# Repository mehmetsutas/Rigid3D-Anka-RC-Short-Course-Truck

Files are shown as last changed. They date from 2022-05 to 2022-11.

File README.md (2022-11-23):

# RIGID3D ANKA 3d Printed 1/10 RC Short Course Truck
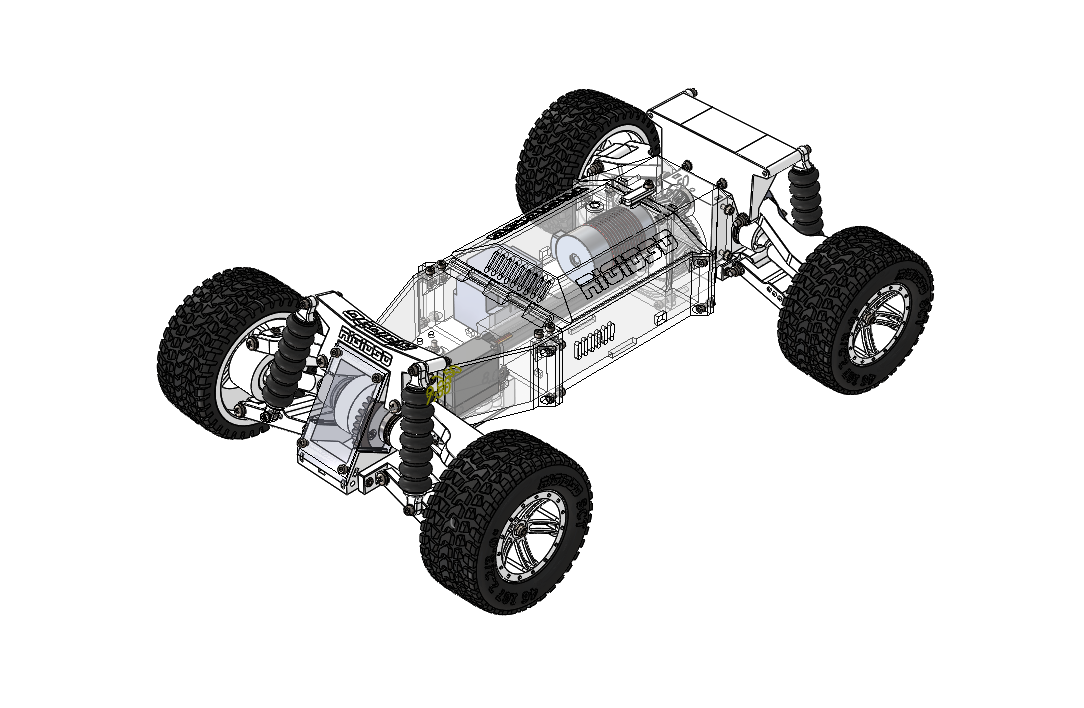
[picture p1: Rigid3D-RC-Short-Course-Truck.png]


Anka is a mostly 3d printed 1/10 RC Short Course Truck which is inspired and remixed from the excellent Tarmo4 project. (You may reach the Tarmo4 project's details from [here](https://www.reddit.com/r/EngineeringNS/).)

If you are a terrible driver like me, this hobby might become a bit expensive. Especially bashers may encounter lots of crashes and breakage which discourages the hobbyist. I wanted to design a basher which is mostly 3d printed so that I can drive it without worrying about crashes and breaks. I enjoy bashing more since I don't have to pay for the spares and wait for them to arrive.

The project is named Anka which is the Turkish equivalent of Phoenix from Greek or Simurgh from Persian mythology. After each crash broken parts are reprinted and the truck is reborn as does the immortal Anka which is reborn from its ashes.

In this model you can even print the shock absorbers and tires with TPU filament. But do not expect the performance of oil filled shocks or rubber tires from them.

Most of the parts may be printed with PLA and should work well with 2600KV motor and 2S LIPO battery. The material tested and recommended are shown in the file notes.

It can be printed on small printers. Most of the parts can be fit in a 15x15x15cm (6"x6"x6") build volume. Only the bumpers require at least 20x20cm (8”x8”) print bed.

The truck is designed in the Short Course Truck (SCT) class. It meets the width and wheelbase dimension specifications of ROAR 1/10 Short Course Truck class.

The steering system is designed according to Ackermann geometry.

3d printed open differentials are used on both front and rear differentials.

Traxxas Slash or Remo Hobby short course truck body would fit on it perfectly. Body can be fixed to the chassis by glueing strong magnets.

You may reach the parametric design files from [github repository](https://github.com/mehmetsutas/Rigid3D-Anka-RC-Short-Course-Truck).

[Here is a test run of Anka.](https://youtu.be/6hFY0XV2smo)

Shield: [][cc-by-sa]

This work is licensed under a
[Creative Commons Attribution-ShareAlike 4.0 International License][cc-by-sa].

[][cc-by-sa]

[cc-by-sa]: http://creativecommons.org/licenses/by-sa/4.0/
[cc-by-sa-image]: https://licensebuttons.net/l/by-sa/4.0/88x31.png
[cc-by-sa-shield]: https://img.shields.io/badge/License-CC%20BY--SA%204.0-lightgrey.svg

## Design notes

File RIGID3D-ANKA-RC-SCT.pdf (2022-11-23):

# RIGID3D ANKA

# 1/10 RC SHORT COURSE TRUCK

English

Version 1.0

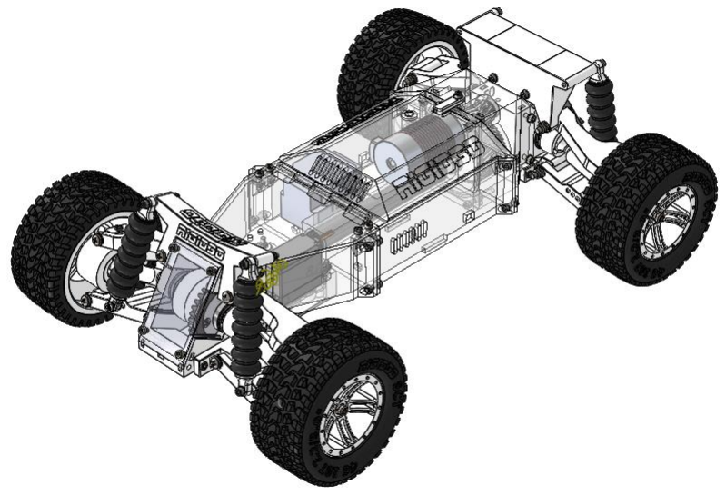
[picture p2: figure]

Rigid3D Anka RC Truck (https://www.rigid3d.com/rigid3d-anka-rc-truck/) © 2022 by Rigid3D is (https://www.rigid3d.com/) licensed under CC BY-SA 4.0 (http://creativecommons.org/licenses/by-sa/4.0/?ref=chooser-v1)

CONTENTS

INTRODUCTION

Anka is a mostly 3d printed 1/10 RC Short Course Truck which is inspired and remixed from the excellent Tarmo4 project. (You may reach the Tarmo4 project's details from here.) (https://www.reddit.com/r/EngineeringNS/)

If you are a terrible driver like me, this hobby might become a bit expensive. Especially bashers may encounter lots of crashes and breakage which discourages the hobbyist. I wanted to design a basher which is mostly 3d printed so that I can drive it without worrying about crashes and breaks. I enjoy bashing more since I don't have to pay for the spares and wait for them to arrive.

The project is named Anka which is the Turkish equivalent of Phoenix from Greek or Simurgh from Persian mythology. After each crash broken parts are reprinted and the truck is reborn as does the immortal Anka which is reborn from its ashes.

In this model you can even print the shock absorbers and tires with TPU filament. But do not expect the performance of oil filled shocks or rubber tires from them.

Most of the parts may be printed with PLA and should work well with 2600KV motor and 2S LIPO battery. The material tested and recommended are shown in the file notes.

It can be printed on small printers. Most of the parts can be fit in a 15x15x15cm (6"x6"x6") build volume. Only the bumpers require at least 20x20cm (8”x8”) print bed.

The truck is designed in the Short Course Truck (SCT) class. It meets the width and wheelbase dimension specifications of ROAR 1/10 Short Course Truck class.

The steering system is designed according to Ackermann geometry.

3d printed open differentials are used on both front and rear differentials.

Traxxas Slash or Remo Hobby short course truck body would fit on it perfectly. Body can be fixed to the chassis by glueing strong magnets.

You may reach the parametric design files from github repository. (https://github.com/mehmetsutas/Rigid3D-Anka-RC-Short-Course-Truck)

LICENSE

Rigid3D Anka RC Truck © 2022 by Rigid3D is licensed under Attribution-ShareAlike 4.0 International. To view a copy of this license, visit http://creativecommons.org/licenses/by-sa/4.0/

LINKS
TARMO4 Project | https://www.reddit.com/r/EngineeringNS/
STL Files | https://www.printables.com/model/214280
GITHUB Repository (STL + Parametric Files) | https://github.com/mehmetsutas/Rigid3D-Anka-RC-Short-Course-Truck
Rigid3D Website (Turkish) | https://www.rigid3d.com
Anka Webpage (under development) | https://www.rigid3d.com/rigid3d-anka-rc-truck/

You may use EngineeringNS subreddit to discuss issues about ANKA along with TARMO4.

SPECIFICATIONS

Class | 1/10 Expert Short Course Truck 4x4
Length | NA (will be available after bumper designs)
Front Track | 296mm (with 3d printed tires)
Rear Track | 296mm (with 3d printed tires)
Center Ground Clearence | 67mm (with 3d printed tires and shocks)
Weight | 2.3kgs (without battery / with 3d printed tires and shocks)
Height | NA (depends on body)
Wheelbase | 321mm
Tire Diameter / Width | 107mm / 46mm
Wheel Diameter | Outer 56mm, Inner 76mm
Drive Ratio | Gearbox 2.625, Differential 2.5, Total 6,5625
Differential | Front & rear 3d printed open type
Drive | Shaft driven
Theoretical Steering Angle | Max. 30˚ (depends on the servo angle. 180˚ servo may steer upto around 27˚)
Caster | 15˚ Positive
Camber | Neutral
Toe | Front Zero, Rear 2.5˚ Toe-in
Battery Compartment Dim. | 122x40x43mm
ESC Compartment Dim. | (122 – Motor Body Length)x40x43mm
Motor Mount | Suitable for Φ36mm brushless or 540/550 brushed motor (Max motor body length 78mm)
Recommended Motor | Brushless 2600KV or lower KV / Brushed 35T or higher turns
Servo Mount Dimensions | 40x20mm servo, distance between mount holes 49x10mm

NEEDED TOOLS

- PH1 Screw Driver
- 5.5 and 7mm Wrench
- 2.5mm Allen Wrench (A short and a long one with ball head is recommended)
- 7mm Socket Wrench (for tightening wheel nuts)
- Drill & 2.5, 3, 4mm drill Bits
- M3 Tap (Optional. There are only a few screws that are directly screwed on plastic.)
- 200 grit sand paper (For cleaning the bearing fit surfaces)
- Hacksaw (for cutting 3mm rod to length)

CONSUMABLES

- PLA filament (more than 1 kg)
- PA12 filament (optional)
- TPU filament
- CA glue
- NLGI00 grade lithium grease⁽*)

(*) NLGI grade determines the viscosity of the grease. 00 grade is low viscous. While NLGI3 grease is like a soap, NLGI00 is like thin jam. It is mainly used in machines with automatic oil pumps for lubricating the linear rails, gears and bearings. It would be hard (at least in Turkey) to find it in small volumes. It is sold in barrels or buckets. But you can produce your own low viscosity grease by mixing a small amount NLGI 2-3 lithium grease with general purpose machine oil or engine oil. The thickness should be like jam. You can use the same mixture to lubricate the linear rails and linear bearings of the 3d printer.

NON-PRINTED PARTS BOM

ITEM NO. | PART | SPECIFICATION | QTY
82 | motor | | 1
102 | servo | | 1
126 | esc | | 1
4/15/37/62/83/117 | 6700 - 15x10x4 bearıng | | 18
13 | 6802 - 15x24x5 bearing | | 4
| Φ3mm steele rod | | 1 meter
30 | wheel-shaft-strength-bar | Φ3mm x 60mm | 4
91 | drive-shaft-strength-bar | Φ3mm x 160mm | 1
2 | planet-gear-pın | Φ3mm x 28mm | 12
24 | shock-pin | Φ3mm x 40mm | 4
105 | rod-ball / 8mm metal bead with 3mm hole | | 4
7/115 | countersunk flat head cross recess screw_ıso | M3 X 30 | 9
103 | countersunk flat head cross recess screw_iso | M3 X 10 | 1
114/138 | countersunk flat head cross recess screw_iso | M3 X 12 | 5
113 | countersunk flat head cross recess screw_iso | M3 X 16 | 2
19/112 | countersunk flat head cross recess screw_iso | M3 X 25 | 6
86/122 | countersunk flat head cross recess screw_iso | M3 X 8 | 10
8/18/52/88/109/129/143/148 | hex nut style 1 gradeab_ıso | M3 | 81
57 | hex nut style 1 gradeab_iso | M4 | 8
55/72 | hex screw gradeab_iso | M4 X 30 | 4
48 | pan head cross recess screw_iso | M4 X 16 | 8
43/79 | pan head cross recess screw_iso | M4 X 35 | 4
58/78 | pan head cross recess screw_iso_2 | M4 X 45 | 8
10/42/75/96/107 | plaın washer normal grade a_ıso | 3 | 62
41/71 | plain washer normal grade a_iso | 4 | 29
20/94/108/127 | socket head cap screw_iso | M3 X 10 | 23
54/74/89/97/123/130/142/147 | socket head cap screw_iso | M3 X 12 | 38
28/51/76/99 | socket head cap screw_iso | M3 X 16 | 17
139 | socket head cap screw_iso | M3 X 20 | 6
45/77 | socket head cap screw_iso | M3 X 25 | 6
44 | socket head cap screw_iso | M3 X 30 | 2
87 | socket set screw cup point_iso | M4 X 5 | 1
9/29/46/121 | torque nut 08_ıso | M3 | 31
47/73 | torque nut 08_iso | M4 | 16
Use any 540/550 sized 35T or higher turn brushed motor or any 2600KV or lower KV Φ36mm inrunner brushless motor. (https://www.aliexpress.com/item/32964687978.html)

For rod balls, stainless steel beads for jewelry making may be used or the balls can be printed. STL for the rod balls can be found at extras folder. (https://www.aliexpress.com/item/33012805327.html)

Links are given for information. Do not consider them as best option.

PRINTED PARTS BOM & PRINT SETTINGS

ITEM NO. | PART | QTY | HEIGHT LAYER | S | INFILL | WALL THICKNESS | MAT. | ORIENTATION
36/63 | axle | 4 | 0,2mm | N | 10 | 3,2mm | PLA
110 | chassis-front | 1 | 0,3mm | N | 10 | 1,6mm | PLA

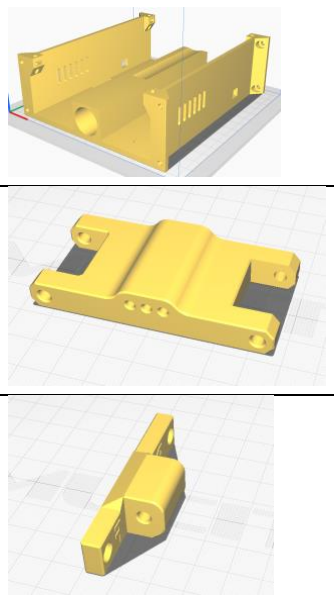
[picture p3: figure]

93 | chassis-middle | 1 | 0,3mm | N | 10 | 1,6mm | PLA
60 | control-arm-lower-BACK | 2 | 0,2mm | N | 10 | 3,2mm | PLA
70 | control-arm-lower-bracket-back-left | 1 | 0,2mm | N | 10 | 3,2mm | PLA (PA12)
69 | control-arm-lower-bracket-back-right | 1 | 0,2mm | N | 10 | 3,2mm | PLA (PA12)
49 | control-arm-lower-bracket-front-left | 1 | 0,2mm | N | 10 | 3,2mm | PLA (PA12)
50 | control-arm-lower-bracket-front-right | 1 | 0,2mm | N | 10 | 3,2mm | PLA (PA12)

ITEM NO. | PART | QTY | HEIGHT LAYER | S | INFILL | WALL THICKNESS | MAT. | ORIENTATION
34 | control-arm-lower-FRONT | 2 | 0,2mm | N | 10 | 3,2mm | PLA

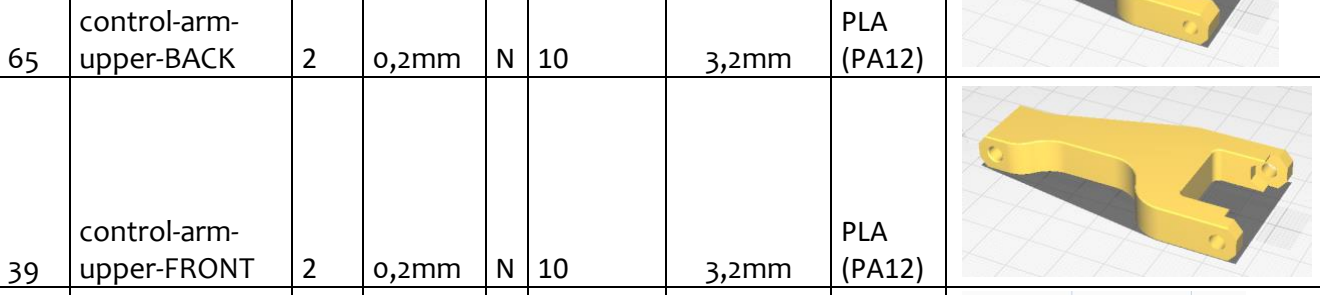
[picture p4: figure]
control-arm-upper-BACK; PLA (PA12); control-arm-upper-FRONT

128 | cover-front | 1 | 0,3mm | N | 10 | 1,6mm | PLA
131 | cover-middle | 1 | 0,3mm | Y | 10 | 1,6mm | PLA
1 | dıfferentıal-housıng-a | 2 | 0,2mm | N | 10 | 3,2mm | PLA
6 | dıfferentıal-housıng-b | 2 | 0,2mm | N | 10 | 3,2mm | PLA
11 | differential-box | 2 | 0,3mm | N | 10 | 1,6mm | PLA

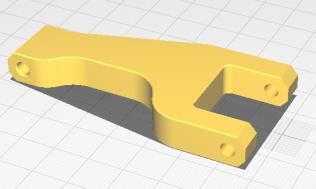
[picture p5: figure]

ITEM NO. | PART | QTY | HEIGHT LAYER | S | INFILL | WALL THICKNESS | MAT. | ORIENTATION
14 | differential-box-lid | 2 | 0,3mm | N | 10 | 1,6mm | PLA
16 | drive-pinion-gear | 2 | 0,2mm | N | 10 | 3,2mm | PLA
90 | drive-shaft | 1 | 0,2mm | N | 10 | 3,2mm | TPU
80 | gear-box | 1 | 0,3mm | N | 10 | 1,6mm | PLA
81 | gear-box-lid | 1 | 0,3mm | N | 10 | 1,6mm | PLA
61 | knuckle-rear | 2 | 0,2mm | N | 10 | 3,2mm | PLA
100 | lock-bar | 1 | 0,2mm | N | 10 | 1,6mm | PLA
3 | planet-gear | 12 | 0,2mm | N | 10 | 3,2mm | PLA

ITEM NO. | PART | QTY | HEIGHT LAYER | S | INFILL | WALL THICKNESS | MAT. | ORIENTATION
25 | rim | 4 | 0,25mm | Y | 10 | 1,6mm | PLA
116 | rod-ball-spacer | 2 | 0,2mm | N | 10 | 1,6mm | PLA
111 | servo-cover | 1 | 0,3mm | N | 10 | 1,6mm | PLA
104 | servo-saver | 1 | 0,2mm | N | 10 | 3,2mm | PLA
119 | servo-saver-SLAVE | 1 | 0,2mm | N | 10 | 3,2mm | PLA
118 | servo-saver-washer | 1 | 0,2mm | N | 10 | 1,6mm | PLA
84 | sg-16-1 | 1 | 0,2mm | N | 10 | 3,2mm | PLA
85 | sg-42-1 | 1 | 0,2mm | N | 10 | 3,2mm | PLA

ITEM NO. | PART | QTY | HEIGHT LAYER | S | INFILL | WALL THICKNESS | MAT. | ORIENTATION
5 | shaft-gear | 4 | 0,2mm | N | 10 | 3,2mm | PLA
23 | shock-eye-A | 4 | 0,2mm | N | 10 | 3,2mm | PLA
22 | shock-eye-B | 4 | 0,2mm | N | 10 | 3,2mm | PLA
66 | shock-tower-back | 1 | 0,3mm | N | 10 | 1,6mm | PLA

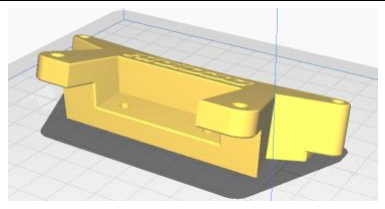
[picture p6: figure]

53 | shock-tower-front | 1 | 0,3mm | Y | 10 | 1,6mm | PLA
120 | steering-center-link | 1 | 0,2mm | N | 10 | 3,2mm | PLA

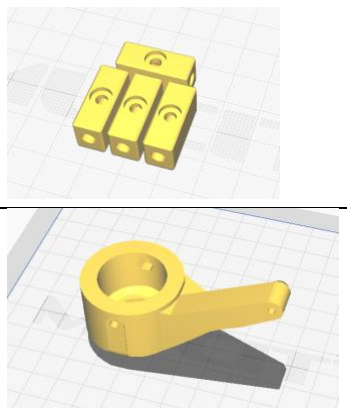
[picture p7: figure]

33 | steering-knuckle-bracket | 4 | 0,2mm | N | 10 | 3,2mm | PLA
32 | steering-knuckle-left | 1 | 0,2mm | N | 10 | 3,2mm | PLA

ITEM NO. | PART | QTY | HEIGHT LAYER | S | INFILL | WALL THICKNESS | MAT. | ORIENTATION
56 | steering-knuckle-right | 1 | 0,2mm | N | 10 | 3,2mm | PLA
106 | steering-linkage⁽*) | 2 | 0,2mm | N | 10 | 3,2mm | PLA

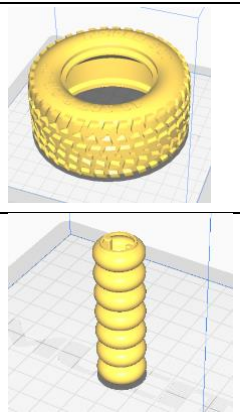
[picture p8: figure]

26 | tire | 4 | 0,25mm | N | 10 | 1,6mm | TPU
21 | tpu-spring | 4 | 0,2mm | N | 10 | 1,6mm | TPU
27 | wheel-shaft | 4 | 0,2mm | N | 10 | 3,2mm | PLA

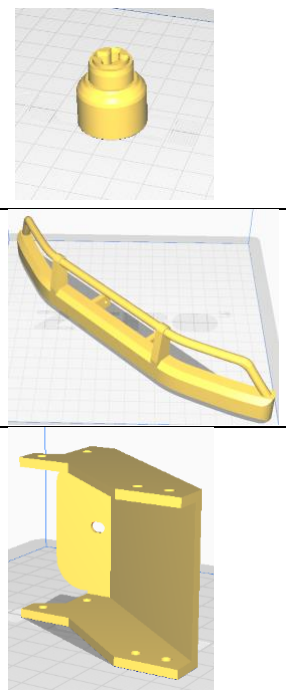
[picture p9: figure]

17 | wheel-shaft-housing | 4 | 0,2mm | N | 10 | 3,2mm | PLA
140 | bumper-bottom-front | 1 | 0,3mm | Y | 10 | 2mm | PLA
141 | bumper-bracket-front | 1 | 0,3mm | Y | 10 | 2mm | PLA

ITEM NO. | PART | QTY | HEIGHT LAYER | S | INFILL | WALL THICKNESS | MAT. | ORIENTATION

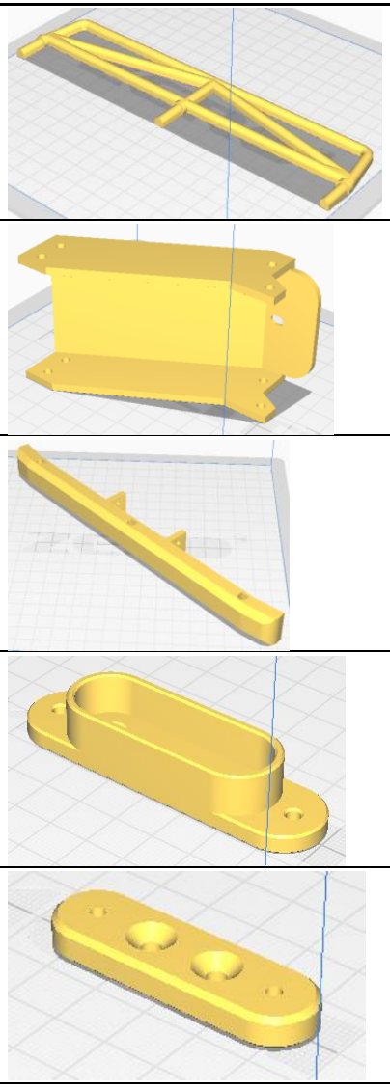
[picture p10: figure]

144 | bumper-rail-back | 1 | 0,2mm | N | 10 | 2mm | PLA
145 | bumper-bracket-back | 1 | 0,3mm | Y | 10 | 2mm | PLA
146 | bumper-bottom-back | 1 | 0,3mm | N | 10 | 2mm | PLA
132 | body-mount-front | 1 | 0,3mm | N | 10 | 2mm | PLA
133 | body-mount-front-body-bracket | 1 | 0,3mm | N | 10 | 2mm | PLA
134 | body-mount-rear | 1 | 0,3mm | N | 10 | 2mm | PLA
135 | body-mount-rear-body-bracket | 1 | 0,3mm | N | 10 | 2mm | PLA

S: Support Needed? Y=Yes / N=No -- MAT.: Material

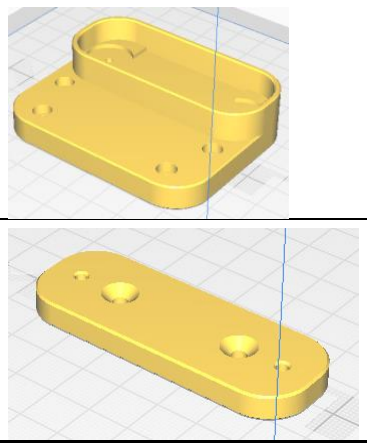
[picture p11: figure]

Although PLA is sufficient for most of the parts on normal operation of the car. It is seen that some parts tend to break more frequently on crashes. It is recommended to print these parts with a nylon blend such as PA12. PA12 is shown in parenthesis as material for these parts.

(*) Print steering linkage in 2 pieces by lowering the model 2.5mm in Z direction into the print bed. Combine 2 halves by screws and nuts after placing the rod balls on the recesses.

EXPLODED DRAWINGS

DIFFERENTIAL INNER ASSY

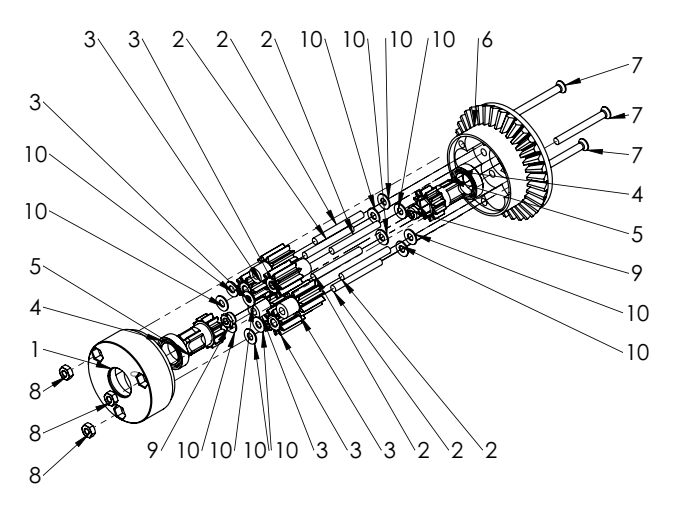
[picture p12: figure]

ITEM NO. | PART | SPECIFICATION | QTY.
1 | dıfferentıal-housıng-a | | 1
2 | planet-gear-pın | Φ3mm x 28mm | 6
3 | planet-gear | | 6
4 | 6700 - 15x10x4 bearıng | | 2
5 | shaft-gear | | 2
6 | dıfferentıal-housıng-b | | 1
7 | countersunk flat head cross recess screw_ıso | M3 X 30 | 3
8 | hex nut style 1 gradeab_ıso | M3 | 3
9 | torque nut 08_ıso | M3 | 2
10 | plaın washer normal grade a_ıso | 3 | 12

Note:

Fill the housing with NLGI00 grade grease.

DIFFERENTIAL ASSY

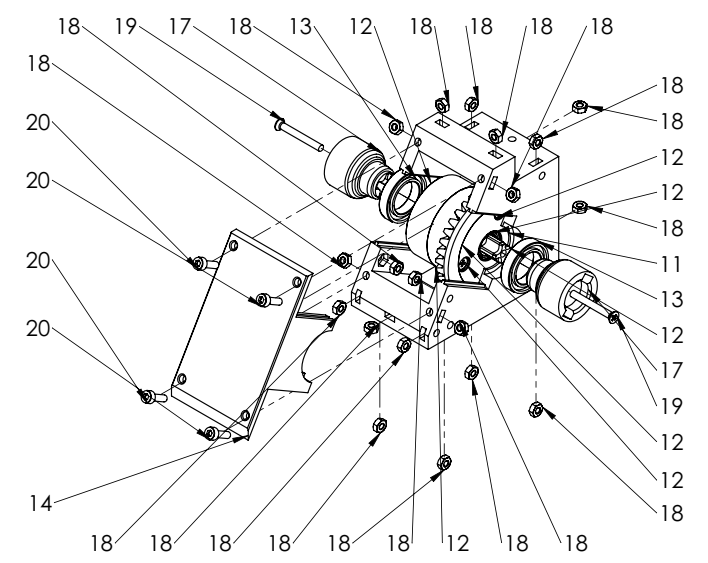
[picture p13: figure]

ITEM NO. | PART | SPECIFICATION | QTY.
11 | differential-box | | 1
12 | differential-inner-assy | | 1
13 | radial ball bearing_68_iso | 15X24X5MM 6802 | 2
14 | differential-box-lid | | 1
15 | 6700 - 15x10x4 Bearing | | 1
16 | drive-pinion-gear | | 1
17 | wheel-shaft-housing | | 2
18 | hex nut style 1 gradeab_iso | M3 | 21
19 | countersunk flat head cross recess screw_iso | M3 X 25 | 2
20 | socket head cap screw_iso | M3 X 10 | 4

Note:

Apply NLGI00 grade grease on the bevel gears.

SHOCK ASSY

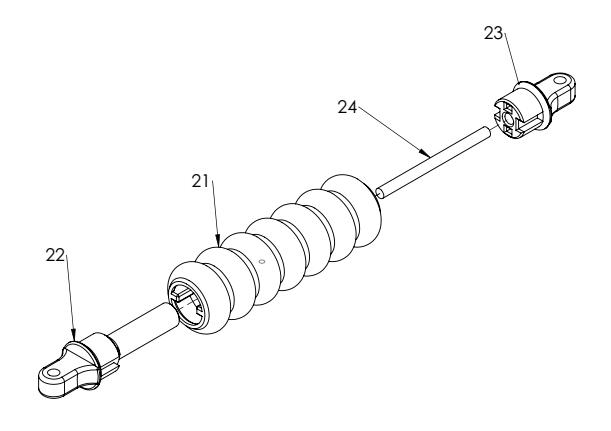
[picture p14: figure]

ITEM NO. | PART | SPECIFICATION | QTY.
21 | tpu-spring | | 1
22 | shock-eye | B | 1
23 | shock-eye | A | 1
24 | shock-pin | Φ3mm x 40mm | 1

Note:

Glue the parts. Pin to shock-eye-A. Shock eyes to tpu-spring.

WHEEL ASSY

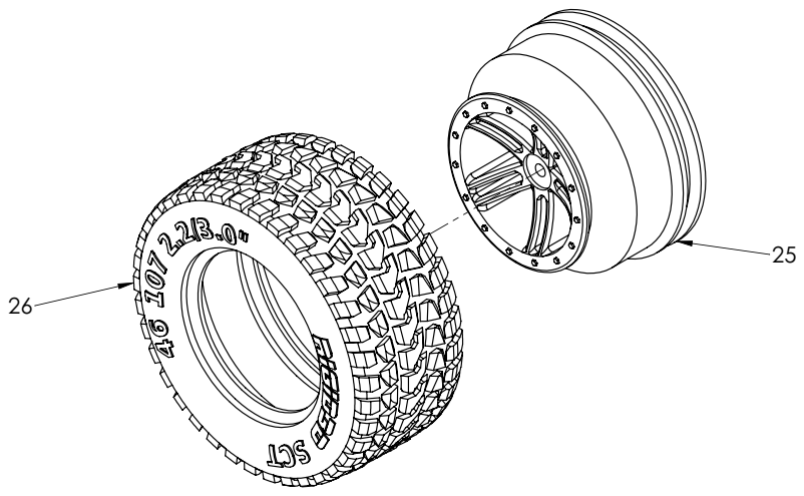
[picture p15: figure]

ITEM NO. | PART | SPECIFICATION | QTY.
25 | rim | | 1
26 | tire | | 1

Notes:

Rim and tire fit very tightly and it requires a lot of force to assemble them together. You may try stepping on the sides of the tire to slide them onto the rim.

WHEEL SHAFT ASSY

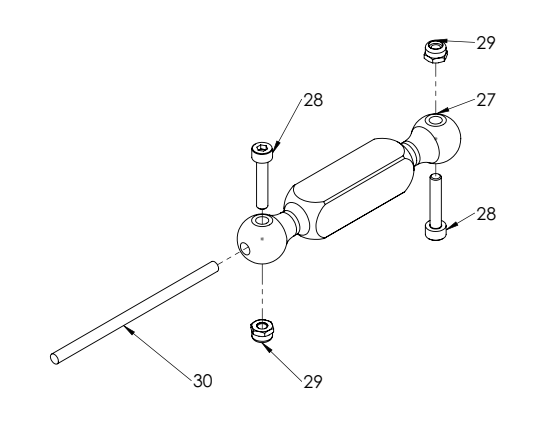
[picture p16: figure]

ITEM NO. | PART | SPECIFICATION | QTY.
27 | wheel-shaft | | 1
28 | socket head cap screw_iso | M3 X 16 | 2
29 | torque nut 08_iso | M3 | 2
30 | wheel-shaft-strength-bar | Φ3mm x 60mm | 1

FRONT ASSY

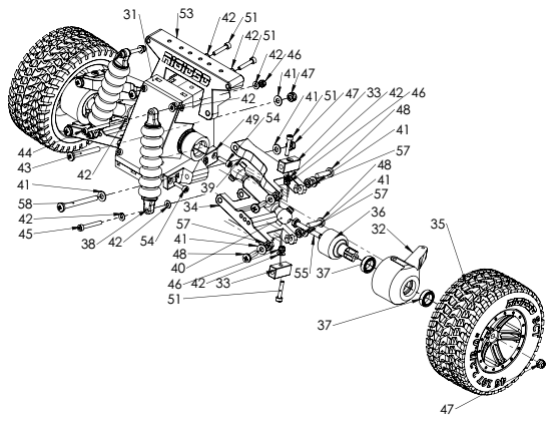
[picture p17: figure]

Notes:

- Only one side is exploded for constraining the sketch size.
- For ease of work, assemble the tires in the last step. Do not install them at this stage of the assembly.

ITEM NO. | PART | SPECIFICATION | QTY.
31 | differential-assy | | 1
32 | steering-knuckle-left | | 1
33 | steering-knuckle-bracket | | 4
34 | control-arm-lower-FRONT | FRONT | 2
35 | wheel-assy | | 2
36 | axle | | 2
37 | 6700 - 15x10x4 Bearing | | 4
38 | shock-assy-V2 | | 2
39 | control-arm-upper-FRONT | FRONT | 2
40 | wheel-shaft-assy | | 2
41 | plain washer normal grade a_iso | 4 | 13
42 | plain washer normal grade a_iso | 3 | 17
43 | pan head cross recess screw_iso | M4 X 35 | 2
44 | socket head cap screw_iso | M3 X 30 | 2
45 | socket head cap screw_iso | M3 X 25 | 2
46 | torque nut 08_iso | M3 | 6
47 | torque nut 08_iso | M4 | 6
48 | pan head cross recess screw_iso | M4 X 16 | 8
49 | control-arm-lower-bracket-front-left | | 1
50 | control-arm-lower-bracket-front-right | | 1
51 | socket head cap screw_iso | M3 X 16 | 6
52 | hex nut style 1 gradeab_iso | M3 | 2
53 | shock-tower-front | | 1
54 | socket head cap screw_iso | M3 X 12 | 4
55 | hex screw gradeab_iso | M4 X 30 | 2
56 | steering-knuckle-right | | 1
57 | hex nut style 1 gradeab_iso | M4 | 8
58 | pan head cross recess screw_iso_2 | M4 X 45 | 2

BACK ASSY

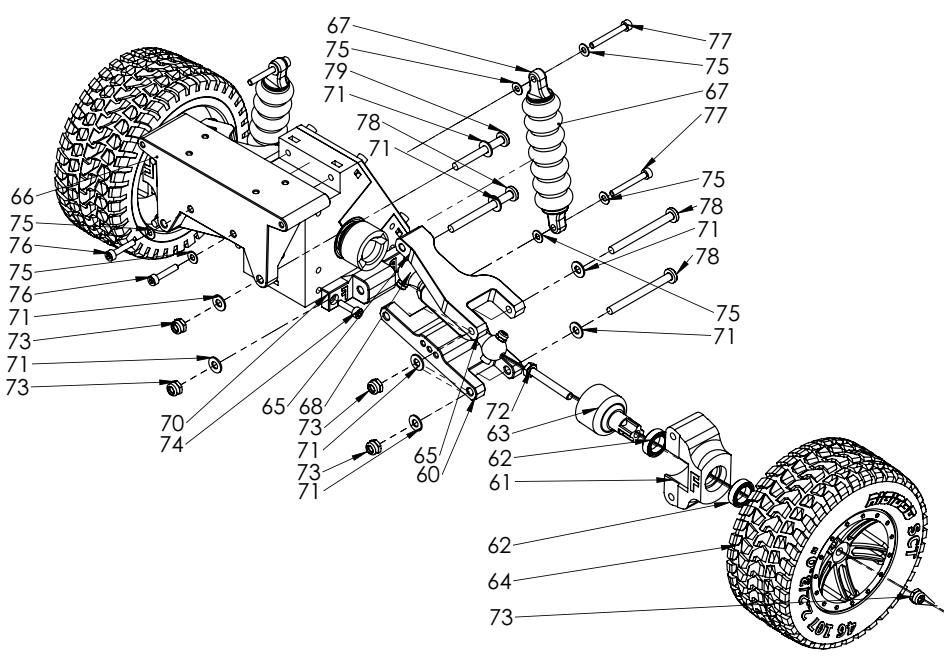
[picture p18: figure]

Notes:

- Only one side is exploded for constraining the sketch size.
- For ease of work, assemble the tires in the last step. Do not install them at this stage of the assembly.

ITEM NO. | PART | SPECIFICATION | QTY.
59 | differential-assy | | 1
60 | control-arm-lower-BACK | BACK | 2
61 | knuckle-rear | | 2
62 | 6700 - 15x10x4 Bearing | | 4
63 | axle | | 2
64 | wheel-assy | | 2
65 | control-arm-upper-BACK | BACK | 2
66 | shock-tower-back | | 1
67 | shock-assy-V2 | | 2
68 | wheel-shaft-assy | | 2
69 | control-arm-lower-bracket-back-right | | 1
70 | control-arm-lower-bracket-back-left | | 1
71 | plain washer normal grade a_iso | 4 | 16
72 | hex screw gradeab_iso | M4 X 30 | 2
73 | torque nut 08_iso | M4 | 10
74 | socket head cap screw_iso | M3 X 12 | 4
75 | plain washer normal grade a_iso | 3 | 10
76 | socket head cap screw_iso | M3 X 16 | 2
77 | socket head cap screw_iso | M3 X 25 | 4
78 | pan head cross recess screw_iso_2 | M4 X 45 | 6
79 | pan head cross recess screw_iso_2 | M4 X 35 | 2

GEAR BOX ASSY

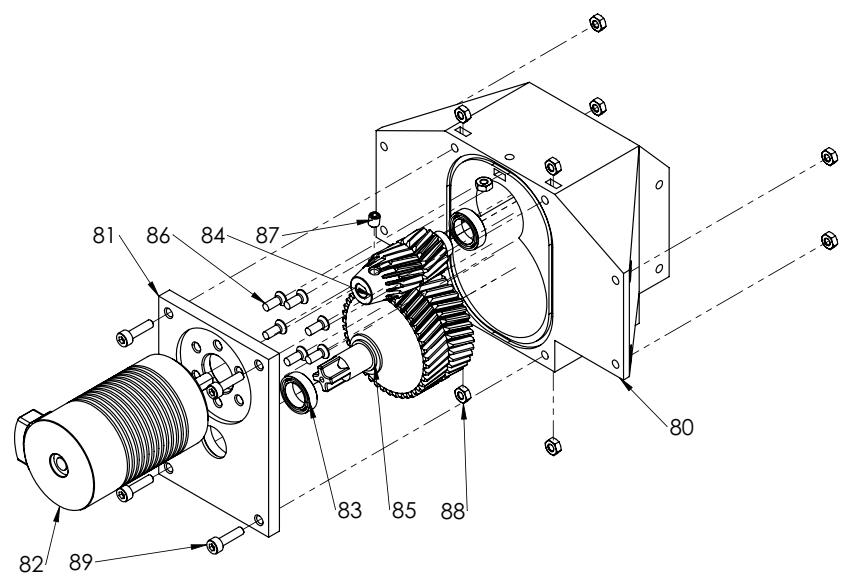
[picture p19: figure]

ITEM NO. | PART | SPECIFICATION | QTY.
80 | gear-box | | 1
81 | gear-box-lid | | 1
82 | motor | | 1
83 | 6700 - 15x10x4 Bearing | | 2
84 | sg-16-1 | 16T-M1 | 1
85 | sg-42-1 | 42T-M1 | 1
86 | countersunk flat head cross recess screw_iso | M3 X 8 | 6
87 | socket set screw cup point_iso | M4 X 5 | 1
88 | hex nut style 1 gradeab_iso | M3 | 9
89 | socket head cap screw_iso | M3 X 12 | 4

Note:

Apply NLGI00 grade grease on the gears.

DRIVE SHAFT ASSY

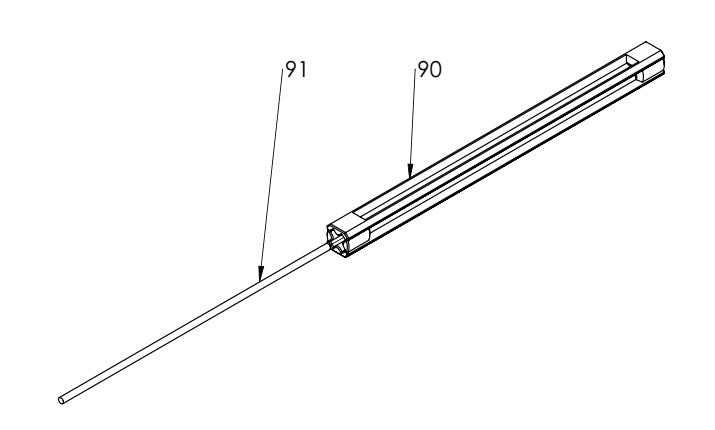
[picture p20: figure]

ITEM NO. | PART | SPECIFICATION | QTY.
90 | drive-shaft | | 1
91 | drive-shaft-strength-bar | Φ3mm x 160mm | 1

RIGID3D SCT BACK ASSY

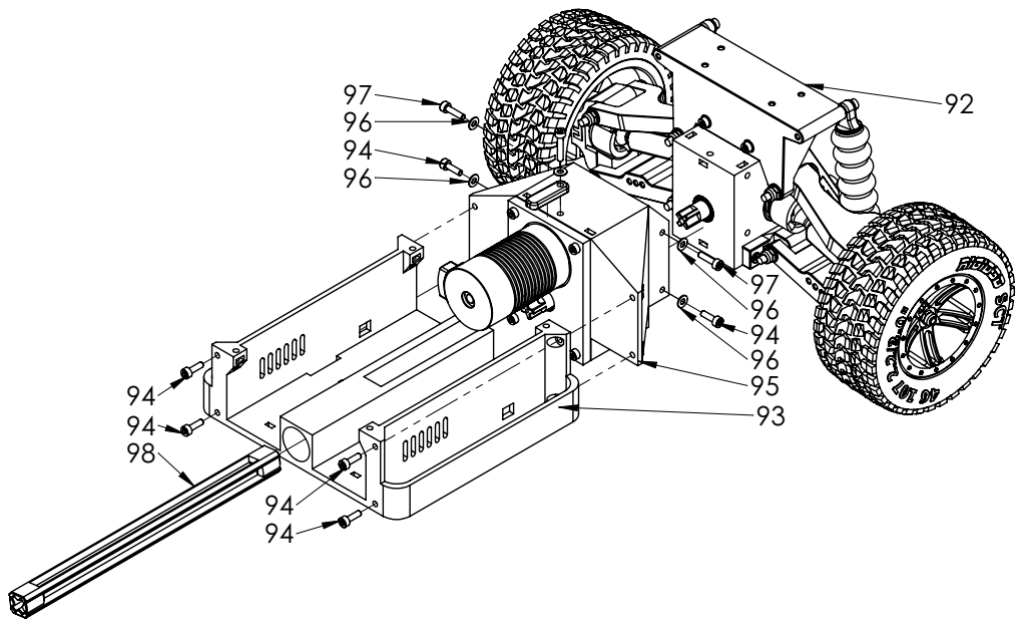
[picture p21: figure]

ITEM NO. | PART | SPECIFICATION | QTY.
92 | back-assy | | 1
93 | chassis-middle | | 1
94 | socket head cap screw_iso | M3 X 10 | 6
95 | gear-box-assy | | 1
96 | plain washer normal grade a_iso | 3 | 5
97 | socket head cap screw_iso | M3 X 12 | 2
98 | drive-shaft-assy | | 1
99 | socket head cap screw_iso | M3 X 16 | 1
100 | lock-bar | | 1

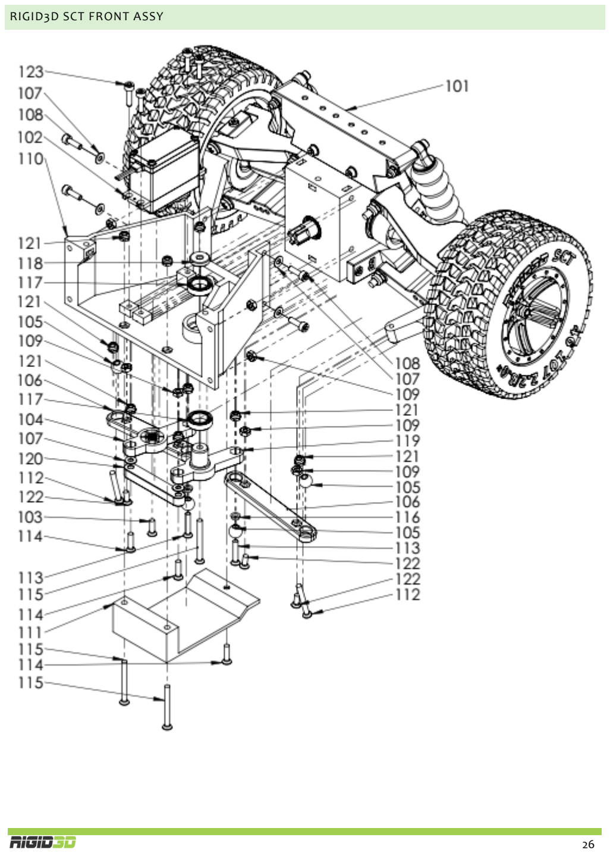
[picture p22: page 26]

RIGID3D SCT FRONT ASSY

ITEM NO. | PART | SPECIFICATION | QTY.
101 | front-assy | | 1
102 | servo | | 1
103 | countersunk flat head cross recess screw_iso | M3 X 10 | 1
104 | servo-saver | | 1
105 | rod-ball | | 4
106 | steering-linkage | | 2
107 | plain washer normal grade a_iso | 3 | 6
108 | socket head cap screw_iso | M3 X 10 | 4
109 | hex nut style 1 gradeab_iso | M3 | 8
110 | chassis-front | | 1
111 | servo-cover | | 1
112 | countersunk flat head cross recess screw_iso | M3 X 25 | 2
113 | countersunk flat head cross recess screw_iso | M3 X 16 | 2
114 | countersunk flat head cross recess screw_iso | M3 X 12 | 3
115 | countersunk flat head cross recess screw_iso | M3 X 30 | 3
116 | rod-ball-spacer | | 2
117 | 6700 - 15x10x4 Bearing | | 2
118 | servo-saver-washer | | 1
119 | servo-saver-SLAVE | SLAVE | 1
120 | steering-center-link | | 1
121 | torque nut 08_iso | M3 | 13
122 | countersunk flat head cross recess screw_iso | M3 X 8 | 4
123 | socket head cap screw_iso | M3 X 12 | 4

RIGID3D SCT V2

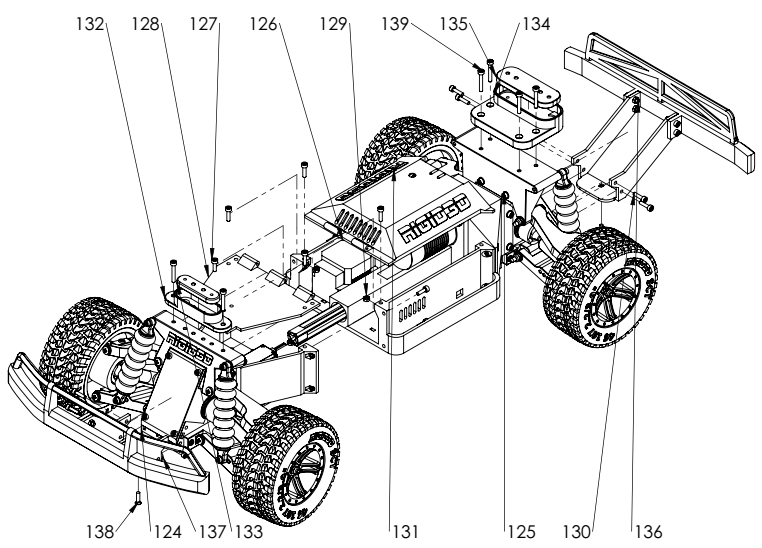
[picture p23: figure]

ITEM NO. | PART | SPECIFICATION | QTY.
124 | rigid3d-sct-front-assy | | 1
125 | rigid3d-sct-back-assy | | 1
126 | esc | | 1
127 | socket head cap screw_iso | M3 X 10 | 5
128 | cover-front | | 1
129 | hex nut style 1 gradeab_iso | M3 | 6
130 | socket head cap screw_iso | M3 X 12 | 12
131 | cover-middle | | 1
132 | body-mount-front | | 1
133 | body-mount-front-body-bracket | | 1
134 | body-mount-rear | | 1
135 | body-mount-rear-body-bracket | | 1
136 | bumper-back | | 1
137 | bumper-front | | 1
138 | countersunk flat head cross recess screw_iso | M3 X 12 | 2
139 | socket head cap screw_iso | M3 X 20 | 6

Note:

Middle cover is hinged. Use a piece of 1.75mm filament as hinge pin.

BUMPER FRONT

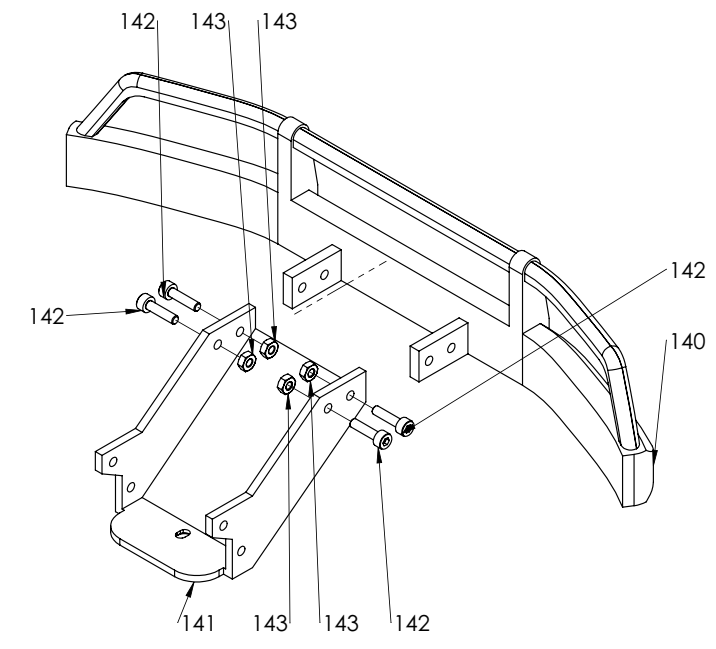
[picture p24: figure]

ITEM NO. | PART | SPECIFICATION | QTY.
140 | bumper-bottom-front | | 1
141 | bumper-bracket-front | | 1
142 | socket head cap screw_iso | M3 X 12 | 4
143 | hex nut style 1 gradeab_iso | M3 | 4

BUMPER BACK

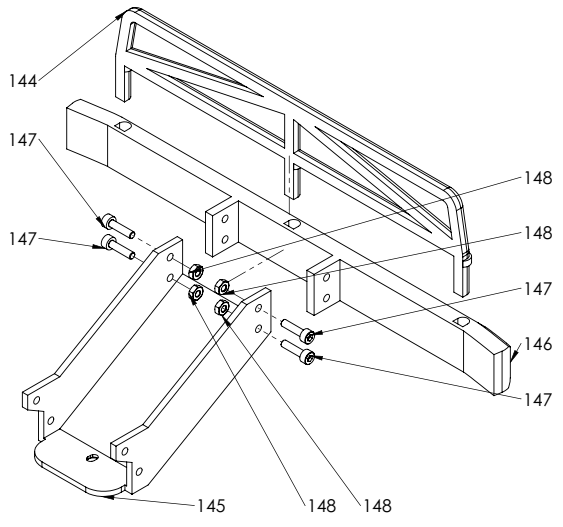
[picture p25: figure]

ITEM NO. | PART | SPECIFICATION | QTY.
144 | bumper-rail-back | | 1
145 | bumper-bracket-back | | 1
146 | bumper-bottom-back | | 1
147 | socket head cap screw_iso | M3 X 12 | 4
148 | hex nut style 1 gradeab_iso | M3 | 4

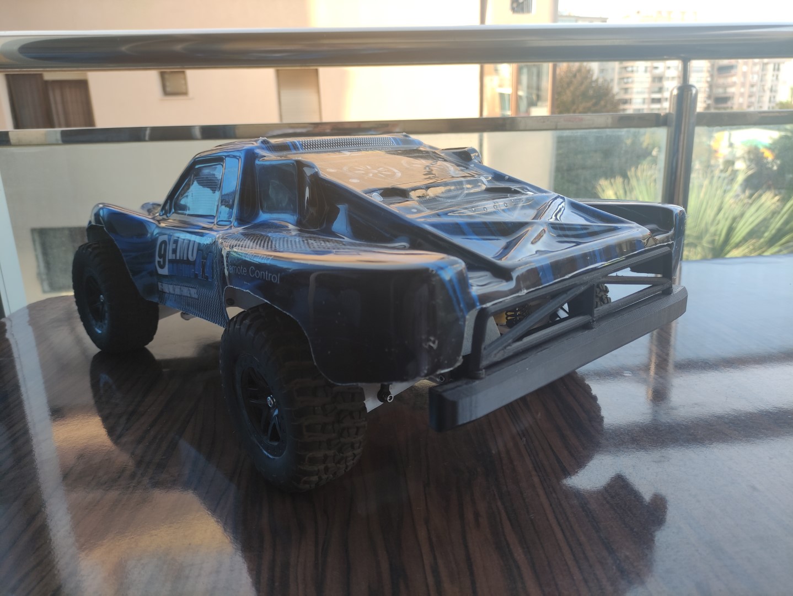
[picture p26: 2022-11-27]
IMG_20221001_175840 (Büyük).jpg

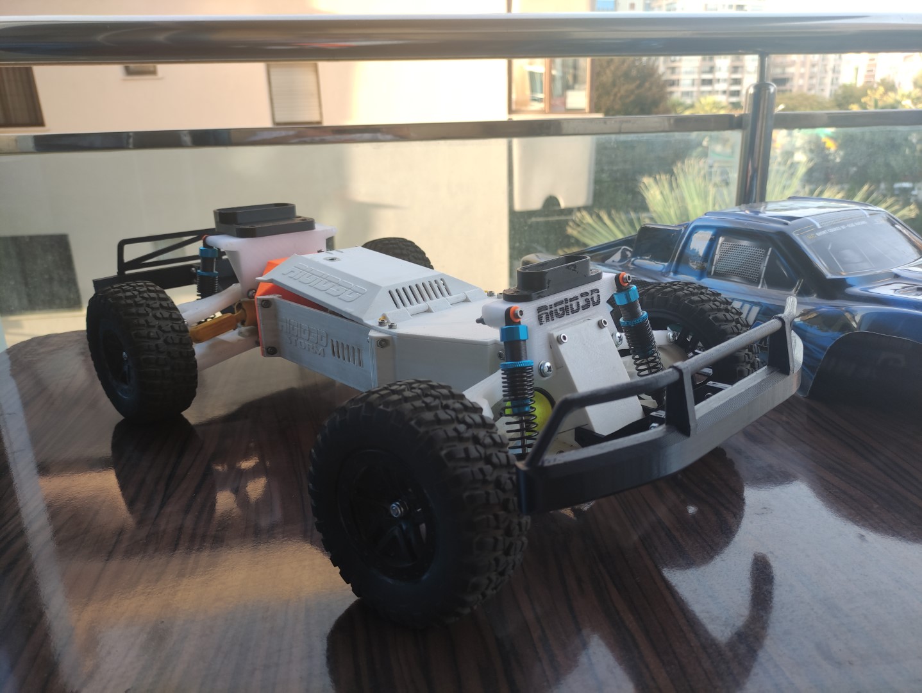
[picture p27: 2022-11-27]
IMG_20221001_175925 (Büyük).jpg

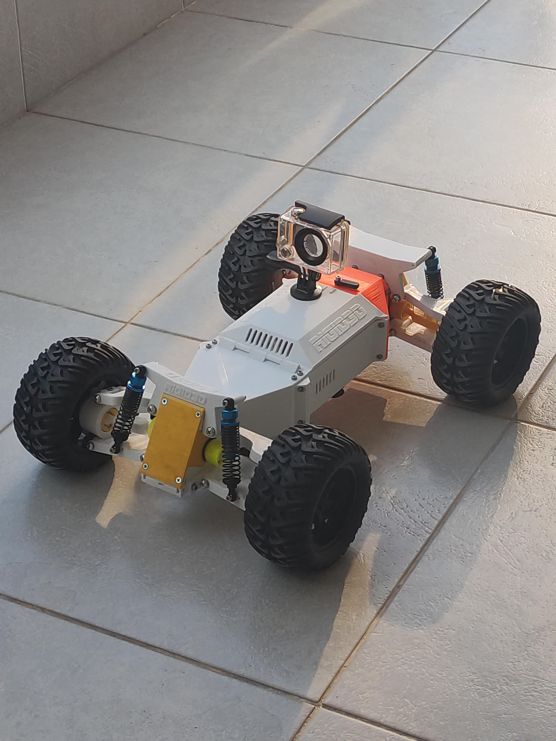
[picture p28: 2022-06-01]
pmxta5gfsnz81.jpg

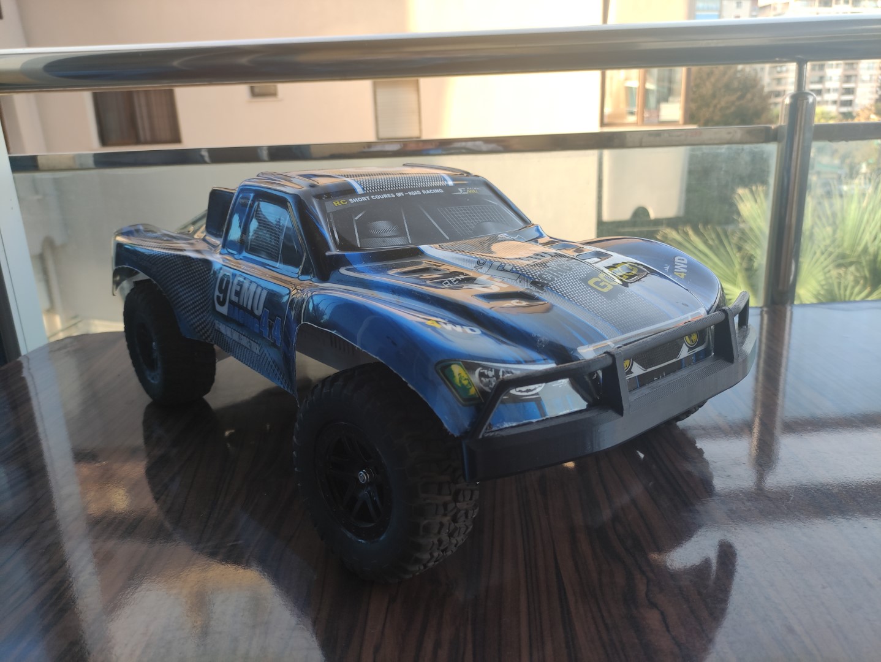
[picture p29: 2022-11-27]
IMG_20221001_175818 (Büyük).jpg

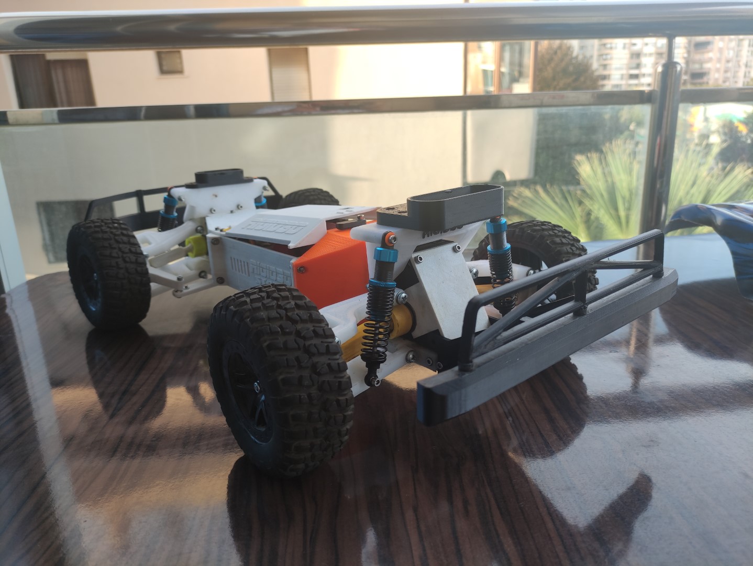
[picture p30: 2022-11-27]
IMG_20221001_175855 (Büyük).jpg

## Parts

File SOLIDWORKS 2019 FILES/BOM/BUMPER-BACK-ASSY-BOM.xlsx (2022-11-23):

ITEM NO. | PART | SPECIFICATION | QTY. | SW-Configuration Name(Configuration Name)
144 | bumper-rail-back |  | 1 | Default
145 | bumper-bracket-back |  | 1 | Default
146 | bumper-bottom-back |  | 1 | Default
147 | socket head cap screw_iso | M3 X 12 | 4 | ISO 4762 M3 x 12 - 12N
148 | hex nut style 1 gradeab_iso | M3 | 4 | ISO - 4032 - M3 - D - N

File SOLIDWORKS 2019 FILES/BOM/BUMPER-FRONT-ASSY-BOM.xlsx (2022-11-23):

ITEM NO. | PART | SPECIFICATION | QTY. | SW-Configuration Name(Configuration Name)
140 | bumper-bottom-front |  | 1 | Default
141 | bumper-bracket-front |  | 1 | Default
142 | socket head cap screw_iso | M3 X 12 | 4 | ISO 4762 M3 x 12 - 12N
143 | hex nut style 1 gradeab_iso | M3 | 4 | ISO - 4032 - M3 - D - N

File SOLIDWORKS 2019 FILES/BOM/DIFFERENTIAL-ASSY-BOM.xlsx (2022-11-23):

ITEM NO. | PART | SPECIFICATION | QTY. | SW-Configuration Name(Configurat ion Name)
11 | differential-box |  | 1 | Default
12 | differential-inner-assy |  | 1 | Default
13 | radial ball bearing_68_iso | 15X24X5MM 6802 | 2 | ISO 15 RBB - 1815 - 18,SI,NC,18_68
14 | differential-box-lid |  | 1 | Default
15 | 6700 - 15x10x4 Bearing |  | 1 | Rolling bearings 63700 GB 276-94
16 | drive-pinion-gear |  | 1 | ISO - Straight bevel pinion 1.5M14PT 37GT 20PA 7FW --- 14O9,9H32MD2.0 N
17 | wheel-shaft-housing |  | 2 | Default
18 | hex nut style 1 gradeab_iso | M3 | 21 | ISO - 4032 - M3 - D - N
19 | countersunk flat head cross recess screw_iso | M3 X 25 | 2 | ISO 7046-1 - M3 x 25 - Z - 25N
20 | socket head cap screw_iso | M3 X 10 | 4 | ISO 4762 M3 x 10 - 10N

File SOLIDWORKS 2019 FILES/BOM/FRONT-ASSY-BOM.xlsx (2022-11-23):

ITEM NO. | PART | SPECIFICATION | QTY. | SW-Configuration Name(Configuration Name)
31 | differential-assy |  | 1 | Default
32 | steering-knuckle-left |  | 1 | Default
33 | steering-knuckle-bracket |  | 4 | Default
34 | control-arm-lower |  | 2 | on
35 | wheel-assy |  | 2 | Default
36 | axle |  | 2 | Default
37 | 6700 - 15x10x4 Bearing |  | 4 | Rolling bearings 63700 GB 276-94
38 | shock-assy-V2 |  | 2 | Default
39 | control-arm-upper |  | 2 | on
40 | wheel-shaft-assy |  | 2 | Default
41 | plain washer normal grade a_iso | 4 | 13 | Washer ISO 7089 - 4
42 | plain washer normal grade a_iso | 3 | 17 | Washer ISO 7089 - 3
43 | pan head cross recess screw_iso | M4 X 35 | 2 | ISO 7045 - M4 x 35 - Z - 35N
44 | socket head cap screw_iso | M3 X 30 | 2 | ISO 4762 M3 x 30 - 18N
45 | socket head cap screw_iso | M3 X 25 | 2 | ISO 4762 M3 x 25 - 18N
46 | torque nut 08_iso | M3 | 6 | ISO 10511-M3-N
47 | torque nut 08_iso | M4 | 6 | ISO 10511-M4-N
48 | pan head cross recess screw_iso | M4 X 16 | 8 | ISO 7045 - M4 x 16 - Z - 16N
49 | control-arm-lower-bracket-front-left |  | 1 | Default
50 | control-arm-lower-bracket-front-right |  | 1 | Default
51 | socket head cap screw_iso | M3 X 16 | 6 | ISO 4762 M3 x 16 - 16N
52 | hex nut style 1 gradeab_iso | M3 | 2 | ISO - 4032 - M3 - D - N
53 | shock-tower-front |  | 1 | Default
54 | socket head cap screw_iso | M3 X 12 | 4 | ISO 4762 M3 x 12 - 12N
55 | hex screw gradeab_iso | M4 X 30 | 2 | ISO 4017 - M4 x 30-N
56 | steering-knuckle-right |  | 1 | Default
57 | hex nut style 1 gradeab_iso | M4 | 8 | ISO - 4032 - M4 - D - N
58 | pan head cross recess screw_iso_2 | M4 X 45 | 2 | ISO 7045 - M4 x 45 - Z - 45N

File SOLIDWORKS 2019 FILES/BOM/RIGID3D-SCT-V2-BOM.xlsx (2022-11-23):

ITEM NO. | PART | SPECIFICATION | QTY. | SW-Configuration Name(Configuration Name)
124 | rigid3d-sct-front-assy |  | 1 | Default
125 | rigid3d-sct-back-assy |  | 1 | Default
126 | esc |  | 1 | Default
127 | socket head cap screw_iso | M3 X 10 | 5 | ISO 4762 M3 x 10 - 10N
128 | cover-front |  | 1 | Default
129 | hex nut style 1 gradeab_iso | M3 | 6 | ISO - 4032 - M3 - D - N
130 | socket head cap screw_iso | M3 X 12 | 12 | ISO 4762 M3 x 12 - 12N
131 | cover-middle |  | 1 | Default
132 | body-mount-front |  | 1 | Default
133 | body-mount-front-body-bracket |  | 1 | Default
134 | body-mount-rear |  | 1 | Default
135 | body-mount-rear-body-bracket |  | 1 | Default
136 | bumper-back |  | 1 | Default
137 | bumper-front |  | 1 | Default
138 | countersunk flat head cross recess screw_iso | M3 X 12 | 2 | ISO 7046-1 - M3 x 12 - Z - 12N
139 | socket head cap screw_iso | M3 X 20 | 6 | ISO 4762 M3 x 20 - 20N

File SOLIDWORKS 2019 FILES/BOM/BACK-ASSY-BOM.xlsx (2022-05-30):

ITEM NO. | PART | SPECIFICATION | QTY. | SW-Configuration Name(Configuration Name)
59 | differential-assy |  | 1 | Default
60 | control-arm-lower |  | 2 | Default
61 | knuckle-rear |  | 2 | Default
62 | 6700 - 15x10x4 Bearing |  | 4 | Rolling bearings 63700 GB 276-94
63 | axle |  | 2 | Default
64 | wheel-assy |  | 2 | Default
65 | control-arm-upper |  | 2 | Default
66 | shock-tower-back |  | 1 | Default
67 | shock-assy-V2 |  | 2 | Default
68 | wheel-shaft-assy |  | 2 | Default
69 | control-arm-lower-bracket-back-right |  | 1 | Default
70 | control-arm-lower-bracket-back-left |  | 1 | Default
71 | plain washer normal grade a_iso | 4 | 16 | Washer ISO 7089 - 4
72 | hex screw gradeab_iso | M4 X 30 | 2 | ISO 4017 - M4 x 30-N
73 | torque nut 08_iso | M4 | 10 | ISO 10511-M4-N
74 | socket head cap screw_iso | M3 X 12 | 4 | ISO 4762 M3 x 12 - 12N
75 | plain washer normal grade a_iso | 3 | 10 | Washer ISO 7089 - 3
76 | socket head cap screw_iso | M3 X 16 | 2 | ISO 4762 M3 x 16 - 16N
77 | socket head cap screw_iso | M3 X 25 | 4 | ISO 4762 M3 x 25 - 18N
78 | pan head cross recess screw_iso_2 | M4 X 45 | 6 | ISO 7045 - M4 x 45 - Z - 45N
79 | pan head cross recess screw_iso_2 | M4 X 35 | 2 | ISO 7045 - M4 x 35 - Z - 35N

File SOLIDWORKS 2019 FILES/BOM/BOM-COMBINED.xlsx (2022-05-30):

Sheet: Sayfa1
ITEM NO. | PART | SPECIFICATION | QTY. | CONF | ÇARPAN | ASSEMBLY | TOTAL QTY
1 | dıfferentıal-housıng-a |  | 1 | SOL | 2 | DIFFERENTIAL INNER ASSY | 2
2 | planet-gear-pın | Φ3mm x 28mm | 6 | DEFAULT | 2 | DIFFERENTIAL INNER ASSY | 12
3 | planet-gear |  | 6 | ISO - SPUR GEAR 1M 10T 20PA 13FW --- S10B7H20L3.0N | 2 | DIFFERENTIAL INNER ASSY | 12
4 | 6700 - 15x10x4 bearıng |  | 2 | ROLLING BEARINGS 63700 GB 276-94 | 2 | DIFFERENTIAL INNER ASSY | 4
5 | shaft-gear |  | 2 | ISO - SPUR GEAR 1M 12T 20PA 6FW --- S12A75H50L3.0N | 2 | DIFFERENTIAL INNER ASSY | 4
6 | dıfferentıal-housıng-b |  | 1 | DEFAULT | 2 | DIFFERENTIAL INNER ASSY | 2
7 | countersunk flat head cross recess screw_ıso | M3 X 30 | 3 | ISO 7046-1 - M3 X 30 - Z - 30N | 2 | DIFFERENTIAL INNER ASSY | 6
8 | hex nut style 1 gradeab_ıso | M3 | 3 | ISO - 4032 - M3 - D - N | 2 | DIFFERENTIAL INNER ASSY | 6
9 | torque nut 08_ıso | M3 | 2 | ISO 10511-M3-N | 2 | DIFFERENTIAL INNER ASSY | 4
10 | plaın washer normal grade a_ıso | 3 | 12 | WASHER ISO 7089 - 3 | 2 | DIFFERENTIAL INNER ASSY | 24
11 | differential-box |  | 1 | Default | 2 | DIFFERENTIAL ASSY | 2
12 | differential-inner-assy |  | 1 | Default | 2 | DIFFERENTIAL ASSY | 2
13 | radial ball bearing_68_iso | 15X24X5MM 6802 | 2 | ISO 15 RBB - 1815 - 18,SI,NC,18_68 | 2 | DIFFERENTIAL ASSY | 4
14 | differential-box-lid |  | 1 | Default | 2 | DIFFERENTIAL ASSY | 2
15 | 6700 - 15x10x4 Bearing |  | 1 | Rolling bearings 63700 GB 276-94 | 2 | DIFFERENTIAL ASSY | 2
16 | drive-pinion-gear |  | 1 | ISO - Straight bevel pinion 1.5M14PT 37GT 20PA 7FW --- 14O9,9H32MD2.0 N | 2 | DIFFERENTIAL ASSY | 2
17 | wheel-shaft-housing |  | 2 | Default | 2 | DIFFERENTIAL ASSY | 4
18 | hex nut style 1 gradeab_iso | M3 | 19 | ISO - 4032 - M3 - D - N | 2 | DIFFERENTIAL ASSY | 38
19 | countersunk flat head cross recess screw_iso | M3 X 25 | 2 | ISO 7046-1 - M3 x 25 - Z - 25N | 2 | DIFFERENTIAL ASSY | 4
20 | socket head cap screw_iso | M3 X 10 | 4 | ISO 4762 M3 x 10 - 10N | 2 | DIFFERENTIAL ASSY | 8
21 | tpu-spring |  | 1 | Default | 4 | SHOCK ASSY | 4
22 | shock-eye | B | 1 | B | 4 | SHOCK ASSY | 4
23 | shock-eye | A | 1 | A | 4 | SHOCK ASSY | 4
24 | shock-pin | Φ3mm x 40mm | 1 | Default | 4 | SHOCK ASSY | 4
25 | rim |  | 1 | Default | 4 | WHEEL ASSY | 4
26 | tire |  | 1 | Default | 4 | WHEEL ASSY | 4
27 | wheel-shaft |  | 1 | Default | 4 | WHEEL SHAFT ASSY | 4
28 | socket head cap screw_iso | M3 X 16 | 2 | ISO 4762 M3 x 16 - 16N | 4 | WHEEL SHAFT ASSY | 8
29 | torque nut 08_iso | M3 | 2 | ISO 10511-M3-N | 4 | WHEEL SHAFT ASSY | 8
30 | wheel-shaft-strength-bar | Φ3mm x 60mm | 1 | Default | 4 | WHEEL SHAFT ASSY | 4
31 | differential-assy |  | 1 | Default | 1 | FRONT ASSY | 1
32 | steering-knuckle-left |  | 1 | Default | 1 | FRONT ASSY | 1
33 | steering-knuckle-bracket |  | 4 | Default | 1 | FRONT ASSY | 4
34 | control-arm-lower-FRONT | FRONT | 2 | on | 1 | FRONT ASSY | 2
35 | wheel-assy |  | 2 | Default | 1 | FRONT ASSY | 2
36 | axle |  | 2 | Default | 1 | FRONT ASSY | 2
37 | 6700 - 15x10x4 Bearing |  | 4 | Rolling bearings 63700 GB 276-94 | 1 | FRONT ASSY | 4
38 | shock-assy-V2 |  | 2 | Default | 1 | FRONT ASSY | 2
39 | control-arm-upper-FRONT | FRONT | 2 | on | 1 | FRONT ASSY | 2
40 | wheel-shaft-assy |  | 2 | Default | 1 | FRONT ASSY | 2
41 | plain washer normal grade a_iso | 4 | 13 | Washer ISO 7089 - 4 | 1 | FRONT ASSY | 13
42 | plain washer normal grade a_iso | 3 | 17 | Washer ISO 7089 - 3 | 1 | FRONT ASSY | 17
43 | pan head cross recess screw_iso | M4 X 35 | 2 | ISO 7045 - M4 x 35 - Z - 35N | 1 | FRONT ASSY | 2
44 | socket head cap screw_iso | M3 X 30 | 2 | ISO 4762 M3 x 30 - 18N | 1 | FRONT ASSY | 2
45 | socket head cap screw_iso | M3 X 25 | 2 | ISO 4762 M3 x 25 - 18N | 1 | FRONT ASSY | 2
46 | torque nut 08_iso | M3 | 6 | ISO 10511-M3-N | 1 | FRONT ASSY | 6
47 | torque nut 08_iso | M4 | 6 | ISO 10511-M4-N | 1 | FRONT ASSY | 6
48 | pan head cross recess screw_iso | M4 X 16 | 8 | ISO 7045 - M4 x 16 - Z - 16N | 1 | FRONT ASSY | 8
49 | control-arm-lower-bracket-front-left |  | 1 | Default | 1 | FRONT ASSY | 1
50 | control-arm-lower-bracket-front-right |  | 1 | Default | 1 | FRONT ASSY | 1
51 | socket head cap screw_iso | M3 X 16 | 6 | ISO 4762 M3 x 16 - 16N | 1 | FRONT ASSY | 6
52 | hex nut style 1 gradeab_iso | M3 | 2 | ISO - 4032 - M3 - D - N | 1 | FRONT ASSY | 2
53 | shock-tower-front |  | 1 | Default | 1 | FRONT ASSY | 1
54 | socket head cap screw_iso | M3 X 12 | 4 | ISO 4762 M3 x 12 - 12N | 1 | FRONT ASSY | 4
55 | hex screw gradeab_iso | M4 X 30 | 2 | ISO 4017 - M4 x 30-N | 1 | FRONT ASSY | 2
56 | steering-knuckle-right |  | 1 | Default | 1 | FRONT ASSY | 1
57 | hex nut style 1 gradeab_iso | M4 | 8 | ISO - 4032 - M4 - D - N | 1 | FRONT ASSY | 8
58 | pan head cross recess screw_iso_2 | M4 X 45 | 2 | ISO 7045 - M4 x 45 - Z - 45N | 1 | FRONT ASSY | 2
59 | differential-assy |  | 1 | Default | 1 | BACK ASSY | 1
60 | control-arm-lower-BACK | BACK | 2 | Default | 1 | BACK ASSY | 2
61 | knuckle-rear |  | 2 | Default | 1 | BACK ASSY | 2
62 | 6700 - 15x10x4 Bearing |  | 4 | Rolling bearings 63700 GB 276-94 | 1 | BACK ASSY | 4
63 | axle |  | 2 | Default | 1 | BACK ASSY | 2
64 | wheel-assy |  | 2 | Default | 1 | BACK ASSY | 2
65 | control-arm-upper-BACK | BACK | 2 | Default | 1 | BACK ASSY | 2
66 | shock-tower-back |  | 1 | Default | 1 | BACK ASSY | 1
67 | shock-assy-V2 |  | 2 | Default | 1 | BACK ASSY | 2
68 | wheel-shaft-assy |  | 2 | Default | 1 | BACK ASSY | 2
69 | control-arm-lower-bracket-back-right |  | 1 | Default | 1 | BACK ASSY | 1
70 | control-arm-lower-bracket-back-left |  | 1 | Default | 1 | BACK ASSY | 1
71 | plain washer normal grade a_iso | 4 | 16 | Washer ISO 7089 - 4 | 1 | BACK ASSY | 16
72 | hex screw gradeab_iso | M4 X 30 | 2 | ISO 4017 - M4 x 30-N | 1 | BACK ASSY | 2
73 | torque nut 08_iso | M4 | 10 | ISO 10511-M4-N | 1 | BACK ASSY | 10
74 | socket head cap screw_iso | M3 X 12 | 4 | ISO 4762 M3 x 12 - 12N | 1 | BACK ASSY | 4
75 | plain washer normal grade a_iso | 3 | 10 | Washer ISO 7089 - 3 | 1 | BACK ASSY | 10
76 | socket head cap screw_iso | M3 X 16 | 2 | ISO 4762 M3 x 16 - 16N | 1 | BACK ASSY | 2
77 | socket head cap screw_iso | M3 X 25 | 4 | ISO 4762 M3 x 25 - 18N | 1 | BACK ASSY | 4
78 | pan head cross recess screw_iso_2 | M4 X 45 | 6 | ISO 7045 - M4 x 45 - Z - 45N | 1 | BACK ASSY | 6
79 | pan head cross recess screw_iso_2 | M4 X 35 | 2 | ISO 7045 - M4 x 35 - Z - 35N | 1 | BACK ASSY | 2
80 | gear-box |  | 1 | A | 1 | GEAR BOX ASSY | 1
81 | gear-box-lid |  | 1 | B | 1 | GEAR BOX ASSY | 1
82 | 3660-BLDC-RC-MOTOR |  | 1 | Default | 1 | GEAR BOX ASSY | 1
83 | 6700 - 15x10x4 Bearing |  | 2 | Rolling bearings 63700 GB 276-94 | 1 | GEAR BOX ASSY | 2
84 | sg-16-1 | 16T-M1 | 1 | Default | 1 | GEAR BOX ASSY | 1
85 | sg-42-1 | 42T-M1 | 1 | Default | 1 | GEAR BOX ASSY | 1
86 | countersunk flat head cross recess screw_iso | M3 X 8 | 6 | ISO 7046-1 - M3 x 8 - Z - 8N | 1 | GEAR BOX ASSY | 6
87 | socket set screw cup point_iso | M4 X 5 | 1 | ISO 4029 - M4 x 5-N | 1 | GEAR BOX ASSY | 1
88 | hex nut style 1 gradeab_iso | M3 | 9 | ISO - 4032 - M3 - D - N | 1 | GEAR BOX ASSY | 9
89 | socket head cap screw_iso | M3 X 12 | 4 | ISO 4762 M3 x 12 - 12N | 1 | GEAR BOX ASSY | 4
90 | drive-shaft |  | 1 | Default | 1 | DRIVE SHAFT ASSY | 1
91 | drive-shaft-strength-bar | Φ3mm x 160mm | 1 | Default | 1 | DRIVE SHAFT ASSY | 1
92 | back-assy |  | 1 | Default | 1 | RIGID3D SCT BACK ASSY | 1
93 | chassis-middle |  | 1 | Default | 1 | RIGID3D SCT BACK ASSY | 1
94 | socket head cap screw_iso | M3 X 10 | 6 | ISO 4762 M3 x 10 - 10N | 1 | RIGID3D SCT BACK ASSY | 6
95 | gear-box-assy |  | 1 | Default | 1 | RIGID3D SCT BACK ASSY | 1
96 | plain washer normal grade a_iso | 3 | 5 | Washer ISO 7089 - 3 | 1 | RIGID3D SCT BACK ASSY | 5
97 | socket head cap screw_iso | M3 X 12 | 2 | ISO 4762 M3 x 12 - 12N | 1 | RIGID3D SCT BACK ASSY | 2
98 | drive-shaft-assy |  | 1 | Default | 1 | RIGID3D SCT BACK ASSY | 1
99 | socket head cap screw_iso | M3 X 16 | 1 | ISO 4762 M3 x 16 - 16N | 1 | RIGID3D SCT BACK ASSY | 1
100 | lock-bar |  | 1 | Default | 1 | RIGID3D SCT BACK ASSY | 1
101 | front-assy |  | 1 | Default | 1 | RIGID3D SCT Front ASSY | 1
102 | TOWER PRO MG-995, ANALOG SERVO |  | 1 | Default | 1 | RIGID3D SCT Front ASSY | 1
103 | countersunk flat head cross recess screw_iso | M3 X 10 | 1 | ISO 7046-1 - M3 x 10 - Z - 10N | 1 | RIGID3D SCT Front ASSY | 1
104 | servo-saver |  | 1 | Default | 1 | RIGID3D SCT Front ASSY | 1
105 | rod-ball |  | 4 | Default | 1 | RIGID3D SCT Front ASSY | 4
106 | steering-linkage |  | 2 | Default | 1 | RIGID3D SCT Front ASSY | 2
107 | plain washer normal grade a_iso | 3 | 6 | Washer ISO 7089 - 3 | 1 | RIGID3D SCT Front ASSY | 6
108 | socket head cap screw_iso | M3 X 10 | 4 | ISO 4762 M3 x 10 - 10N | 1 | RIGID3D SCT Front ASSY | 4
109 | hex nut style 1 gradeab_iso | M3 | 8 | ISO - 4032 - M3 - D - N | 1 | RIGID3D SCT Front ASSY | 8
110 | chassis-front |  | 1 | Default | 1 | RIGID3D SCT Front ASSY | 1
111 | servo-cover |  | 1 | Default | 1 | RIGID3D SCT Front ASSY | 1
112 | countersunk flat head cross recess screw_iso | M3 X 25 | 2 | ISO 7046-1 - M3 x 25 - Z - 25N | 1 | RIGID3D SCT Front ASSY | 2
113 | countersunk flat head cross recess screw_iso | M3 X 16 | 2 | ISO 7046-1 - M3 x 16 - Z - 16N | 1 | RIGID3D SCT Front ASSY | 2
114 | countersunk flat head cross recess screw_iso | M3 X 12 | 3 | ISO 7046-1 - M3 x 12 - Z - 12N | 1 | RIGID3D SCT Front ASSY | 3
115 | countersunk flat head cross recess screw_iso | M3 X 30 | 3 | ISO 7046-1 - M3 x 30 - Z - 30N | 1 | RIGID3D SCT Front ASSY | 3
116 | rod-ball-spacer |  | 2 | Default | 1 | RIGID3D SCT Front ASSY | 2
117 | 6700 - 15x10x4 Bearing |  | 2 | Rolling bearings 63700 GB 276-94 | 1 | RIGID3D SCT Front ASSY | 2
118 | servo-saver-washer |  | 1 | Default | 1 | RIGID3D SCT Front ASSY | 1
119 | servo-saver |  | 1 | Avare | 1 | RIGID3D SCT Front ASSY | 1
120 | steering-center-link |  | 1 | Default | 1 | RIGID3D SCT Front ASSY | 1
121 | torque nut 08_iso | M3 | 13 | ISO 10511-M3-N | 1 | RIGID3D SCT Front ASSY | 13
122 | countersunk flat head cross recess screw_iso | M3 X 8 | 4 | ISO 7046-1 - M3 x 8 - Z - 8N | 1 | RIGID3D SCT Front ASSY | 4
123 | socket head cap screw_iso | M3 X 12 | 4 | ISO 4762 M3 x 12 - 12N | 1 | RIGID3D SCT Front ASSY | 4
124 | rigid3d-sct-front-assy |  | 1 | Default | 1 | RIGID3D SCT V2 | 1
125 | rigid3d-sct-back-assy |  | 1 | Default | 1 | RIGID3D SCT V3 | 1
126 | esc |  | 1 | Default | 1 | RIGID3D SCT V4 | 1
127 | socket head cap screw_iso | M3 X 10 | 5 | ISO 4762 M3 x 10 - 10N | 1 | RIGID3D SCT V5 | 5
128 | cover-front |  | 1 | Default | 1 | RIGID3D SCT V6 | 1
129 | hex nut style 1 gradeab_iso | M3 | 6 | ISO - 4032 - M3 - D - N | 1 | RIGID3D SCT V7 | 6
130 | socket head cap screw_iso | M3 X 12 | 4 | ISO 4762 M3 x 12 - 12N | 1 | RIGID3D SCT V8 | 4
131 | cover-middle |  | 1 | Default | 1 | RIGID3D SCT V9 | 1

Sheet: Sayfa2
ITEM NO. | PART | SPECIFICATION | TOTAL QTY | CONF | ÇARPAN | ASSEMBLY | QTY. | PRINTED
36/63 | axle |  | 4 | Default | 1 | FRONT ASSY | 2 | Y
110 | chassis-front |  | 1 | Default | 1 | RIGID3D SCT Front ASSY | 1 | Y
93 | chassis-middle |  | 1 | Default | 1 | RIGID3D SCT BACK ASSY | 1 | Y
60 | control-arm-lower-BACK | BACK | 2 | Default | 1 | BACK ASSY | 2 | Y
70 | control-arm-lower-bracket-back-left |  | 1 | Default | 1 | BACK ASSY | 1 | Y
69 | control-arm-lower-bracket-back-right |  | 1 | Default | 1 | BACK ASSY | 1 | Y
49 | control-arm-lower-bracket-front-left |  | 1 | Default | 1 | FRONT ASSY | 1 | Y
50 | control-arm-lower-bracket-front-right |  | 1 | Default | 1 | FRONT ASSY | 1 | Y
34 | control-arm-lower-FRONT | FRONT | 2 | on | 1 | FRONT ASSY | 2 | Y
65 | control-arm-upper-BACK | BACK | 2 | Default | 1 | BACK ASSY | 2 | Y
39 | control-arm-upper-FRONT | FRONT | 2 | on | 1 | FRONT ASSY | 2 | Y
128 | cover-front |  | 1 | Default | 1 | RIGID3D SCT V6 | 1 | Y
131 | cover-middle |  | 1 | Default | 1 | RIGID3D SCT V9 | 1 | Y
1 | dıfferentıal-housıng-a |  | 2 | SOL | 2 | DIFFERENTIAL INNER ASSY | 1 | Y
6 | dıfferentıal-housıng-b |  | 2 | DEFAULT | 2 | DIFFERENTIAL INNER ASSY | 1 | Y
11 | differential-box |  | 2 | Default | 2 | DIFFERENTIAL ASSY | 1 | Y
14 | differential-box-lid |  | 2 | Default | 2 | DIFFERENTIAL ASSY | 1 | Y
16 | drive-pinion-gear |  | 2 | ISO - Straight bevel pinion 1.5M14PT 37GT 20PA 7FW --- 14O9,9H32MD2.0 N | 2 | DIFFERENTIAL ASSY | 1 | Y
90 | drive-shaft |  | 1 | Default | 1 | DRIVE SHAFT ASSY | 1 | Y
80 | gear-box |  | 1 | A | 1 | GEAR BOX ASSY | 1 | Y
81 | gear-box-lid |  | 1 | B | 1 | GEAR BOX ASSY | 1 | Y
61 | knuckle-rear |  | 2 | Default | 1 | BACK ASSY | 2 | Y
100 | lock-bar |  | 1 | Default | 1 | RIGID3D SCT BACK ASSY | 1 | Y
3 | planet-gear |  | 12 | ISO - SPUR GEAR 1M 10T 20PA 13FW --- S10B7H20L3.0N | 2 | DIFFERENTIAL INNER ASSY | 6 | Y
25 | rim |  | 4 | Default | 4 | WHEEL ASSY | 1 | Y
116 | rod-ball-spacer |  | 2 | Default | 1 | RIGID3D SCT Front ASSY | 2 | Y
111 | servo-cover |  | 1 | Default | 1 | RIGID3D SCT Front ASSY | 1 | Y
104 | servo-saver |  | 1 | Default | 1 | RIGID3D SCT Front ASSY | 1 | Y
119 | servo-saver-SLAVE | SLAVE | 1 | Avare | 1 | RIGID3D SCT Front ASSY | 1 | Y
118 | servo-saver-washer |  | 1 | Default | 1 | RIGID3D SCT Front ASSY | 1 | Y
84 | sg-16-1 | 16T-M1 | 1 | Default | 1 | GEAR BOX ASSY | 1 | Y
85 | sg-42-1 | 42T-M1 | 1 | Default | 1 | GEAR BOX ASSY | 1 | Y
5 | shaft-gear |  | 4 | ISO - SPUR GEAR 1M 12T 20PA 6FW --- S12A75H50L3.0N | 2 | DIFFERENTIAL INNER ASSY | 2 | Y
23 | shock-eye | A | 4 | A | 4 | SHOCK ASSY | 1 | Y
22 | shock-eye | B | 4 | B | 4 | SHOCK ASSY | 1 | Y
66 | shock-tower-back |  | 1 | Default | 1 | BACK ASSY | 1 | Y
53 | shock-tower-front |  | 1 | Default | 1 | FRONT ASSY | 1 | Y
120 | steering-center-link |  | 1 | Default | 1 | RIGID3D SCT Front ASSY | 1 | Y
33 | steering-knuckle-bracket |  | 4 | Default | 1 | FRONT ASSY | 4 | Y
32 | steering-knuckle-left |  | 1 | Default | 1 | FRONT ASSY | 1 | Y
56 | steering-knuckle-right |  | 1 | Default | 1 | FRONT ASSY | 1 | Y
106 | steering-linkage |  | 2 | Default | 1 | RIGID3D SCT Front ASSY | 2 | Y
26 | tire |  | 4 | Default | 4 | WHEEL ASSY | 1 | Y
21 | tpu-spring |  | 4 | Default | 4 | SHOCK ASSY | 1 | Y
27 | wheel-shaft |  | 4 | Default | 4 | WHEEL SHAFT ASSY | 1 | Y
17 | wheel-shaft-housing |  | 4 | Default | 2 | DIFFERENTIAL ASSY | 2 | Y
82 | motor |  | 1 | Default | 1 | GEAR BOX ASSY | 1 | N
4/15/37/62/83/117 | 6700 - 15x10x4 bearıng |  | 18 | ROLLING BEARINGS 63700 GB 276-94 | 2 | DIFFERENTIAL INNER ASSY | 2 | N
7/115 | countersunk flat head cross recess screw_ıso | M3 X 30 | 9 | ISO 7046-1 - M3 X 30 - Z - 30N | 2 | DIFFERENTIAL INNER ASSY | 3 | N
103 | countersunk flat head cross recess screw_iso | M3 X 10 | 1 | ISO 7046-1 - M3 x 10 - Z - 10N | 1 | RIGID3D SCT Front ASSY | 1 | N
114 | countersunk flat head cross recess screw_iso | M3 X 12 | 3 | ISO 7046-1 - M3 x 12 - Z - 12N | 1 | RIGID3D SCT Front ASSY | 3 | N
113 | countersunk flat head cross recess screw_iso | M3 X 16 | 2 | ISO 7046-1 - M3 x 16 - Z - 16N | 1 | RIGID3D SCT Front ASSY | 2 | N
19/112 | countersunk flat head cross recess screw_iso | M3 X 25 | 6 | ISO 7046-1 - M3 x 25 - Z - 25N | 2 | DIFFERENTIAL ASSY | 2 | N
86/122 | countersunk flat head cross recess screw_iso | M3 X 8 | 10 | ISO 7046-1 - M3 x 8 - Z - 8N | 1 | GEAR BOX ASSY | 6 | N
91 | drive-shaft-strength-bar | Φ3mm x 160mm | 1 | Default | 1 | DRIVE SHAFT ASSY | 1 | N
126 | esc |  | 1 | Default | 1 | RIGID3D SCT V4 | 1 | N
8/18/52/88/109/129 | hex nut style 1 gradeab_ıso | M3 | 69 | ISO - 4032 - M3 - D - N | 2 | DIFFERENTIAL INNER ASSY | 3 | N
57 | hex nut style 1 gradeab_iso | M4 | 8 | ISO - 4032 - M4 - D - N | 1 | FRONT ASSY | 8 | N
55/72 | hex screw gradeab_iso | M4 X 30 | 4 | ISO 4017 - M4 x 30-N | 1 | FRONT ASSY | 2 | N
48 | pan head cross recess screw_iso | M4 X 16 | 8 | ISO 7045 - M4 x 16 - Z - 16N | 1 | FRONT ASSY | 8 | N
43/79 | pan head cross recess screw_iso | M4 X 35 | 4 | ISO 7045 - M4 x 35 - Z - 35N | 1 | FRONT ASSY | 2 | N
58/78 | pan head cross recess screw_iso_2 | M4 X 45 | 8 | ISO 7045 - M4 x 45 - Z - 45N | 1 | FRONT ASSY | 2 | N
10/42/75/96/107 | plaın washer normal grade a_ıso | 3 | 62 | WASHER ISO 7089 - 3 | 2 | DIFFERENTIAL INNER ASSY | 12 | N
41/71 | plain washer normal grade a_iso | 4 | 29 | Washer ISO 7089 - 4 | 1 | FRONT ASSY | 13 | N
2 | planet-gear-pın | Φ3mm x 28mm | 12 | DEFAULT | 2 | DIFFERENTIAL INNER ASSY | 6 | N
13 | radial ball bearing_68_iso | 15X24X5MM 6802 | 4 | ISO 15 RBB - 1815 - 18,SI,NC,18_68 | 2 | DIFFERENTIAL ASSY | 2 | N
105 | rod-ball |  | 4 | Default | 1 | RIGID3D SCT Front ASSY | 4 | N
24 | shock-pin | Φ3mm x 40mm | 4 | Default | 4 | SHOCK ASSY | 1 | N
20/94/108/127 | socket head cap screw_iso | M3 X 10 | 23 | ISO 4762 M3 x 10 - 10N | 2 | DIFFERENTIAL ASSY | 4 | N
54/74/89/97/123/130 | socket head cap screw_iso | M3 X 12 | 22 | ISO 4762 M3 x 12 - 12N | 1 | FRONT ASSY | 4 | N
28/51/76/99 | socket head cap screw_iso | M3 X 16 | 17 | ISO 4762 M3 x 16 - 16N | 4 | WHEEL SHAFT ASSY | 2 | N
45/77 | socket head cap screw_iso | M3 X 25 | 6 | ISO 4762 M3 x 25 - 18N | 1 | FRONT ASSY | 2 | N
44 | socket head cap screw_iso | M3 X 30 | 2 | ISO 4762 M3 x 30 - 18N | 1 | FRONT ASSY | 2 | N
87 | socket set screw cup point_iso | M4 X 5 | 1 | ISO 4029 - M4 x 5-N | 1 | GEAR BOX ASSY | 1 | N
9/29/46/121 | torque nut 08_ıso | M3 | 31 | ISO 10511-M3-N | 2 | DIFFERENTIAL INNER ASSY | 2 | N
47/73 | torque nut 08_iso | M4 | 16 | ISO 10511-M4-N | 1 | FRONT ASSY | 6 | N
102 | servo |  | 1 | Default | 1 | RIGID3D SCT Front ASSY | 1 | N
30 | wheel-shaft-strength-bar | Φ3mm x 60mm | 4 | Default | 4 | WHEEL SHAFT ASSY | 1 | N

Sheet: NON PRINTED
ITEM NO. | PART | SPECIFICATION | TOTAL QTY | LINK
82 | motor |  | 1 | https://www.aliexpress.com/item/32964687978.html
102 | servo |  | 1
126 | esc |  | 1 | https://www.aliexpress.com/item/32964687978.html
4/15/37/62/83/117 | 6700 - 15x10x4 bearıng |  | 18 | https://www.aliexpress.com/item/632542696.html
13 | 6802 - 15x24x5 bearing | 15X24X5MM 6802 | 4 | https://www.aliexpress.com/item/1266397116.html
 | Φ3mm steele rod |  | 1 meter
30 | wheel-shaft-strength-bar | Φ3mm x 60mm | 4
91 | drive-shaft-strength-bar | Φ3mm x 160mm | 1
2 | planet-gear-pın | Φ3mm x 28mm | 12
24 | shock-pin | Φ3mm x 40mm | 4
105 | rod-ball / 8mm metal bead with 3mm hole |  | 4 | https://www.aliexpress.com/item/33012805327.html
7/115 | countersunk flat head cross recess screw_ıso | M3 X 30 | 9
103 | countersunk flat head cross recess screw_iso | M3 X 10 | 1
114 | countersunk flat head cross recess screw_iso | M3 X 12 | 3
113 | countersunk flat head cross recess screw_iso | M3 X 16 | 2
19/112 | countersunk flat head cross recess screw_iso | M3 X 25 | 6
86/122 | countersunk flat head cross recess screw_iso | M3 X 8 | 10
8/18/52/88/109/129 | hex nut style 1 gradeab_ıso | M3 | 69
57 | hex nut style 1 gradeab_iso | M4 | 8
55/72 | hex screw gradeab_iso | M4 X 30 | 4
48 | pan head cross recess screw_iso | M4 X 16 | 8
43/79 | pan head cross recess screw_iso | M4 X 35 | 4
58/78 | pan head cross recess screw_iso_2 | M4 X 45 | 8
10/42/75/96/107 | plaın washer normal grade a_ıso | 3 | 62
41/71 | plain washer normal grade a_iso | 4 | 29
20/94/108/127 | socket head cap screw_iso | M3 X 10 | 23
54/74/89/97/123/130 | socket head cap screw_iso | M3 X 12 | 22
28/51/76/99 | socket head cap screw_iso | M3 X 16 | 17
45/77 | socket head cap screw_iso | M3 X 25 | 6
44 | socket head cap screw_iso | M3 X 30 | 2
87 | socket set screw cup point_iso | M4 X 5 | 1
9/29/46/121 | torque nut 08_ıso | M3 | 31
47/73 | torque nut 08_iso | M4 | 16

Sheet: PRINTED
ITEM NO. | PART | QTY | LAYER HEIGHT | SUPPORT | INFILL | WALL THICKNESS | ORIENTATION
36/63 | axle | 4 | 0,2mm | N | 10 | 3,2mm
110 | chassis-front | 1 | 0,3mm | N | 10 | 1,6mm
93 | chassis-middle | 1 | 0,3mm | N | 10 | 1,6mm
60 | control-arm-lower-BACK | 2 | 0,2mm | N | 10 | 3,2mm
70 | control-arm-lower-bracket-back-left | 1 | 0,2mm | N | 10 | 3,2mm
69 | control-arm-lower-bracket-back-right | 1 | 0,2mm | N | 10 | 3,2mm
49 | control-arm-lower-bracket-front-left | 1 | 0,2mm | N | 10 | 3,2mm
50 | control-arm-lower-bracket-front-right | 1 | 0,2mm | N | 10 | 3,2mm
34 | control-arm-lower-FRONT | 2 | 0,2mm | N | 10 | 3,2mm
65 | control-arm-upper-BACK | 2 | 0,2mm | N | 10 | 3,2mm
39 | control-arm-upper-FRONT | 2 | 0,2mm | N | 10 | 3,2mm
128 | cover-front | 1 | 0,3mm | N | 10 | 1,6mm
131 | cover-middle | 1 | 0,3mm | Y | 10 | 1,6mm
1 | dıfferentıal-housıng-a | 2 | 0,2mm | N | 10 | 3,2mm
6 | dıfferentıal-housıng-b | 2 | 0,2mm | N | 10 | 3,2mm
11 | differential-box | 2 | 0,3mm | N | 10 | 1,6mm
14 | differential-box-lid | 2 | 0,3mm | N | 10 | 1,6mm
16 | drive-pinion-gear | 2 | 0,2mm | N | 10 | 3,2mm
90 | drive-shaft | 1 | 0,2mm | N | 10 | 3,2mm
80 | gear-box | 1 | 0,3mm | N | 10 | 1,6mm
81 | gear-box-lid | 1 | 0,3mm | N | 10 | 1,6mm
61 | knuckle-rear | 2 | 0,2mm | N | 10 | 3,2mm
100 | lock-bar | 1 | 0,2mm | N | 10 | 1,6mm
3 | planet-gear | 12 | 0,2mm | N | 10 | 3,2mm
25 | rim | 4 | 0,25mm | Y | 10 | 1,6mm
116 | rod-ball-spacer | 2 | 0,2mm | N | 10 | 1,6mm
111 | servo-cover | 1 | 0,3mm | N | 10 | 1,6mm
104 | servo-saver | 1 | 0,2mm | N | 10 | 3,2mm
119 | servo-saver-SLAVE | 1 | 0,2mm | N | 10 | 3,2mm
118 | servo-saver-washer | 1 | 0,2mm | N | 10 | 1,6mm
84 | sg-16-1 | 1 | 0,2mm | N | 10 | 3,2mm
85 | sg-42-1 | 1 | 0,2mm | N | 10 | 3,2mm
5 | shaft-gear | 4 | 0,2mm | N | 10 | 3,2mm
23 | shock-eye-A | 4 | 0,2mm | N | 10 | 3,2mm
22 | shock-eye-B | 4 | 0,2mm | N | 10 | 3,2mm
66 | shock-tower-back | 1 | 0,3mm | N | 10 | 1,6mm
53 | shock-tower-front | 1 | 0,3mm | Y | 10 | 1,6mm
120 | steering-center-link | 1 | 0,2mm | N | 10 | 3,2mm
33 | steering-knuckle-bracket | 4 | 0,2mm | N | 10 | 3,2mm
32 | steering-knuckle-left | 1 | 0,2mm | N | 10 | 3,2mm
56 | steering-knuckle-right | 1 | 0,2mm | N | 10 | 3,2mm
106 | steering-linkage | 2 | 0,2mm | N | 10 | 3,2mm
26 | tire | 4 | 0,25mm | N | 10 | 1,6mm
21 | tpu-spring | 4 | 0,2mm | N | 10 | 1,6mm
27 | wheel-shaft | 4 | 0,2mm | N | 10 | 3,2mm
17 | wheel-shaft-housing | 4 | 0,2mm | N | 10 | 3,2mm

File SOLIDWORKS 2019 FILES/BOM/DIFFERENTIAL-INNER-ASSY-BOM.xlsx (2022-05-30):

ITEM NO. | PART | SPECIFICATION | QTY. | CONF
1 | DIFFERENTIAL-HOUSING-A |  | 1 | SOL
2 | PLANET-GEAR-PIN |  | 6 | DEFAULT
3 | PLANET-GEAR |  | 6 | ISO - SPUR GEAR 1M 10T 20PA 13FW --- S10B7H20L3.0N
4 | 6700 - 15X10X4 BEARING |  | 2 | ROLLING BEARINGS 63700 GB 276-94
5 | SHAFT-GEAR |  | 2 | ISO - SPUR GEAR 1M 12T 20PA 6FW --- S12A75H50L3.0N
6 | DIFFERENTIAL-HOUSING-B |  | 1 | DEFAULT
7 | COUNTERSUNK FLAT HEAD CROSS RECESS SCREW_ISO | M3 X 30 | 3 | ISO 7046-1 - M3 X 30 - Z - 30N
8 | HEX NUT STYLE 1 GRADEAB_ISO | M3 | 3 | ISO - 4032 - M3 - D - N
9 | TORQUE NUT 08_ISO | M3 | 2 | ISO 10511-M3-N
10 | PLAIN WASHER NORMAL GRADE A_ISO | 3 | 12 | WASHER ISO 7089 - 3

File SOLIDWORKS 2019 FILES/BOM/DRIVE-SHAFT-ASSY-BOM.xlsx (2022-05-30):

ITEM NO. | PART | SPECIFICATION | QTY. | SW-Configuration Name(Configuration Name)
90 | drive-shaft |  | 1 | Default
91 | drive-shaft-strength-bar | Φ3mm x 160mm | 1 | Default

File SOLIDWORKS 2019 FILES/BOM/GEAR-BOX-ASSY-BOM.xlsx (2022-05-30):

ITEM NO. | PART | SPECIFICATION | QTY. | SW-Configuration Name(Configuration Name)
80 | gear-box |  | 1 | A
81 | gear-box |  | 1 | B
82 | 3660-BLDC-RC-MOTOR |  | 1 | Default
83 | 6700 - 15x10x4 Bearing |  | 2 | Rolling bearings 63700 GB 276-94
84 | sg-16-1 | 16T-M1 | 1 | Default
85 | sg-42-1 | 42T-M1 | 1 | Default
86 | countersunk flat head cross recess screw_iso | M3 X 8 | 6 | ISO 7046-1 - M3 x 8 - Z - 8N
87 | socket set screw cup point_iso | M4 X 5 | 1 | ISO 4029 - M4 x 5-N
88 | hex nut style 1 gradeab_iso | M3 | 9 | ISO - 4032 - M3 - D - N
89 | socket head cap screw_iso | M3 X 12 | 4 | ISO 4762 M3 x 12 - 12N

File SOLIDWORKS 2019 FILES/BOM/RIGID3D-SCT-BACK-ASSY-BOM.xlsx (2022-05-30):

ITEM NO. | PART | SPECIFICATION | QTY. | SW-Configuration Name(Configuration Name)
92 | back-assy |  | 1 | Default
93 | chassis-middle |  | 1 | Default
94 | socket head cap screw_iso | M3 X 10 | 6 | ISO 4762 M3 x 10 - 10N
95 | gear-box-assy |  | 1 | Default
96 | plain washer normal grade a_iso | 3 | 5 | Washer ISO 7089 - 3
97 | socket head cap screw_iso | M3 X 12 | 2 | ISO 4762 M3 x 12 - 12N
98 | drive-shaft-assy |  | 1 | Default
99 | socket head cap screw_iso | M3 X 16 | 1 | ISO 4762 M3 x 16 - 16N
100 | lock-bar |  | 1 | Default

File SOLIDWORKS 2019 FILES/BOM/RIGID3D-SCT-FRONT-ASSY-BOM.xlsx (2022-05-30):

ITEM NO. | PART | SPECIFICATION | QTY. | SW-Configuration Name(Configuration Name)
101 | front-assy |  | 1 | Default
102 | TOWER PRO MG-995, ANALOG SERVO |  | 1 | Default
103 | countersunk flat head cross recess screw_iso | M3 X 10 | 1 | ISO 7046-1 - M3 x 10 - Z - 10N
104 | servo-saver |  | 1 | Default
105 | rod-ball |  | 4 | Default
106 | steering-linkage |  | 2 | Default
107 | plain washer normal grade a_iso | 3 | 6 | Washer ISO 7089 - 3
108 | socket head cap screw_iso | M3 X 10 | 4 | ISO 4762 M3 x 10 - 10N
109 | hex nut style 1 gradeab_iso | M3 | 8 | ISO - 4032 - M3 - D - N
110 | chassis-front |  | 1 | Default
111 | servo-cover |  | 1 | Default
112 | countersunk flat head cross recess screw_iso | M3 X 25 | 2 | ISO 7046-1 - M3 x 25 - Z - 25N
113 | countersunk flat head cross recess screw_iso | M3 X 16 | 2 | ISO 7046-1 - M3 x 16 - Z - 16N
114 | countersunk flat head cross recess screw_iso | M3 X 12 | 3 | ISO 7046-1 - M3 x 12 - Z - 12N
115 | countersunk flat head cross recess screw_iso | M3 X 30 | 3 | ISO 7046-1 - M3 x 30 - Z - 30N
116 | rod-ball-spacer |  | 2 | Default
117 | 6700 - 15x10x4 Bearing |  | 2 | Rolling bearings 63700 GB 276-94
118 | servo-saver-washer |  | 1 | Default
119 | servo-saver |  | 1 | Avare
120 | steering-center-link |  | 1 | Default
121 | torque nut 08_iso | M3 | 13 | ISO 10511-M3-N
122 | countersunk flat head cross recess screw_iso | M3 X 8 | 4 | ISO 7046-1 - M3 x 8 - Z - 8N
123 | socket head cap screw_iso | M3 X 12 | 4 | ISO 4762 M3 x 12 - 12N

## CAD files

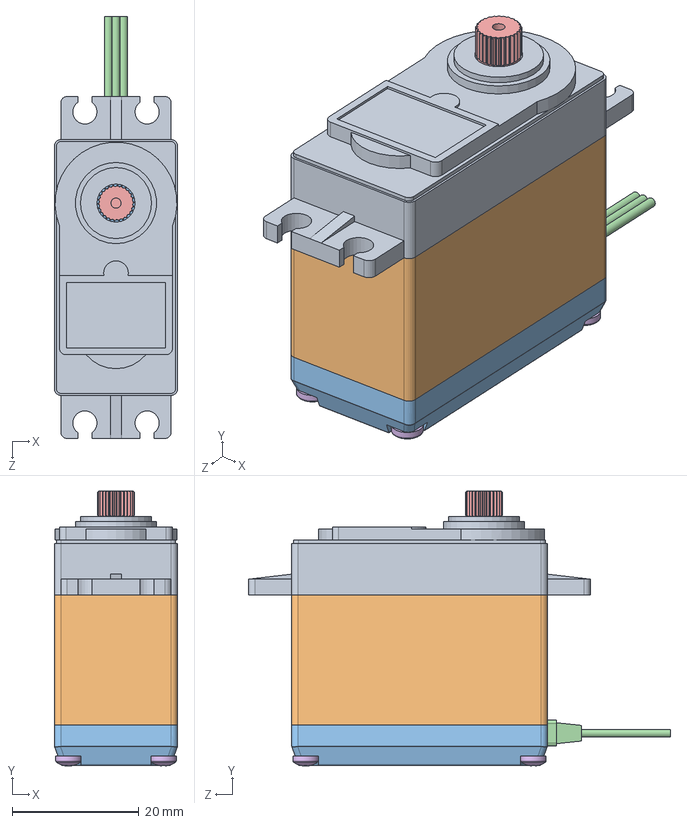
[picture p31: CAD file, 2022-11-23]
SOLIDWORKS 2019 FILES/TOWER PRO MG-995, ANALOG SERVO.SLDASM
19.4 x 43.3 x 66.5 mm
TOWER PRO MG-995, ANALOG SERVO, BODY, TOP-V2
TOWER PRO MG-995, ANALOG SERVO, BODY, MIDDLE-V2
TOWER PRO MG-995, ANALOG SERVO, BODY, BOTTOM-V2
TOWER PRO MG-995, ANALOG SERVO, CONNECTOR-V2
TOWER PRO MG-995, ANALOG SERVO, SHAFT-V2
pan cross head_am x 4

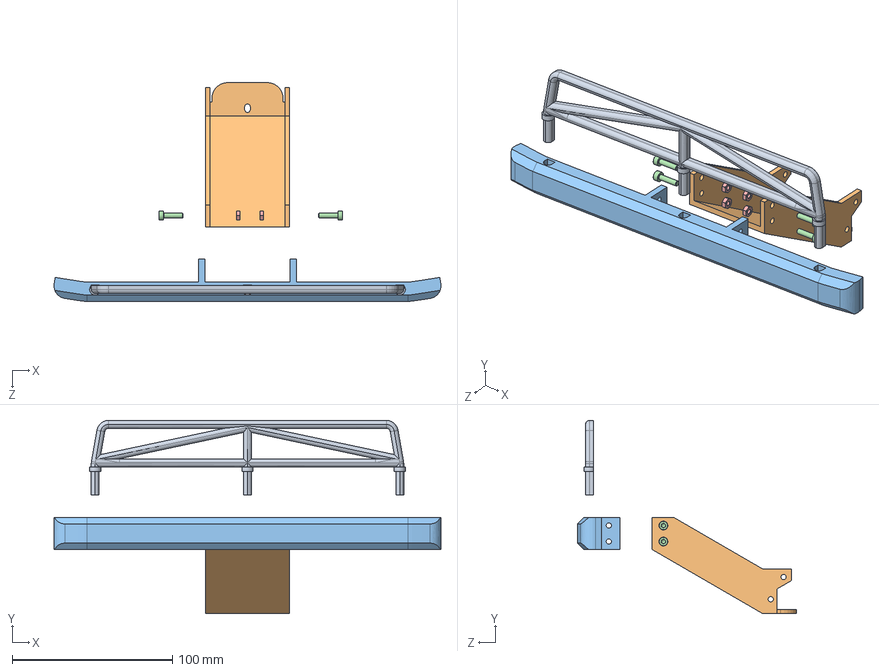
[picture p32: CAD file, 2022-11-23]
SOLIDWORKS 2019 FILES/bumper-back.SLDASM
241.4 x 120.6 x 136.6 mm
bumper-rail-back
bumper-bracket-back
bumper-bottom-back
socket head cap screw_iso x 4
hex nut style 1 gradeab_iso x 4

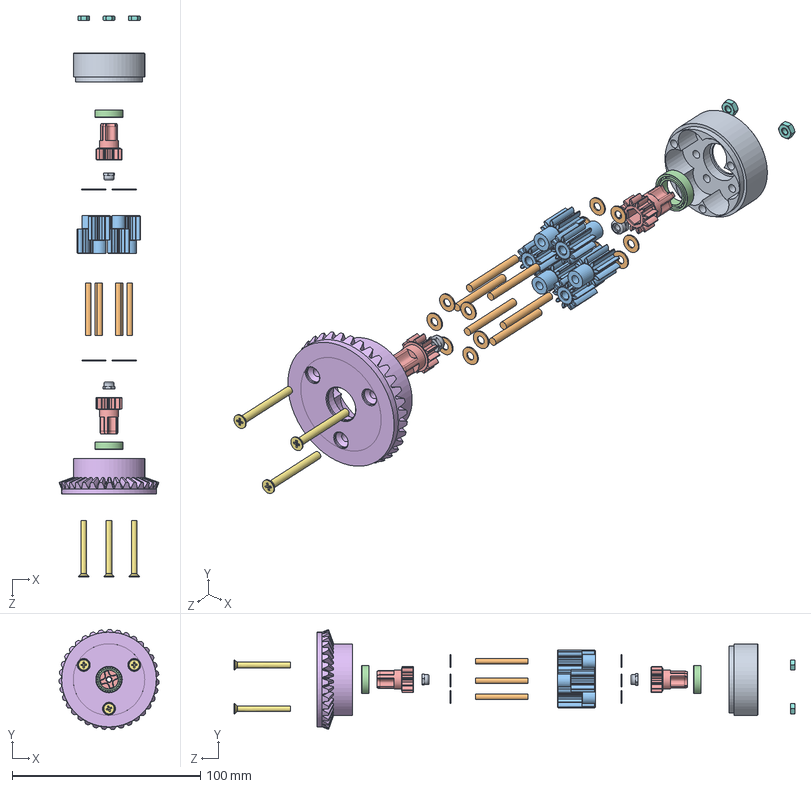
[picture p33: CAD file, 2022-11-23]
SOLIDWORKS 2019 FILES/differential-inner-assy.SLDASM
53.2 x 53.1 x 298.1 mm
differential-housing-a
planet-gear-pin x 6
planet-gear x 6
6700 - 15x10x4 Bearing x 2
shaft-gear x 2
differential-housing-b
countersunk flat head cross recess screw_iso x 3
hex nut style 1 gradeab_iso x 3
torque nut 08_iso x 2
plain washer normal grade a_iso x 12

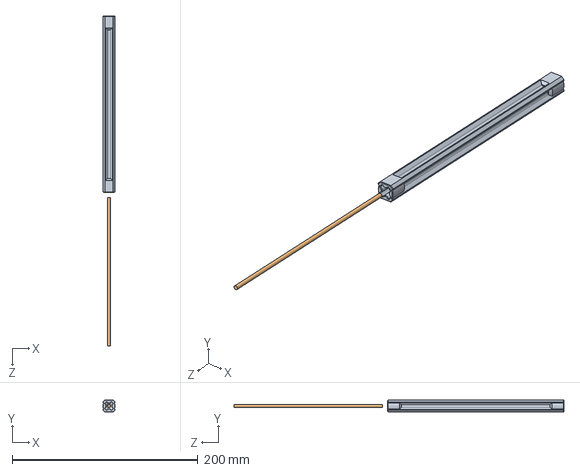
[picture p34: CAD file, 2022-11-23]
SOLIDWORKS 2019 FILES/drive-shaft-assy.SLDASM
13.0 x 13.0 x 355.6 mm
drive-shaft
drive-shaft-strength-bar

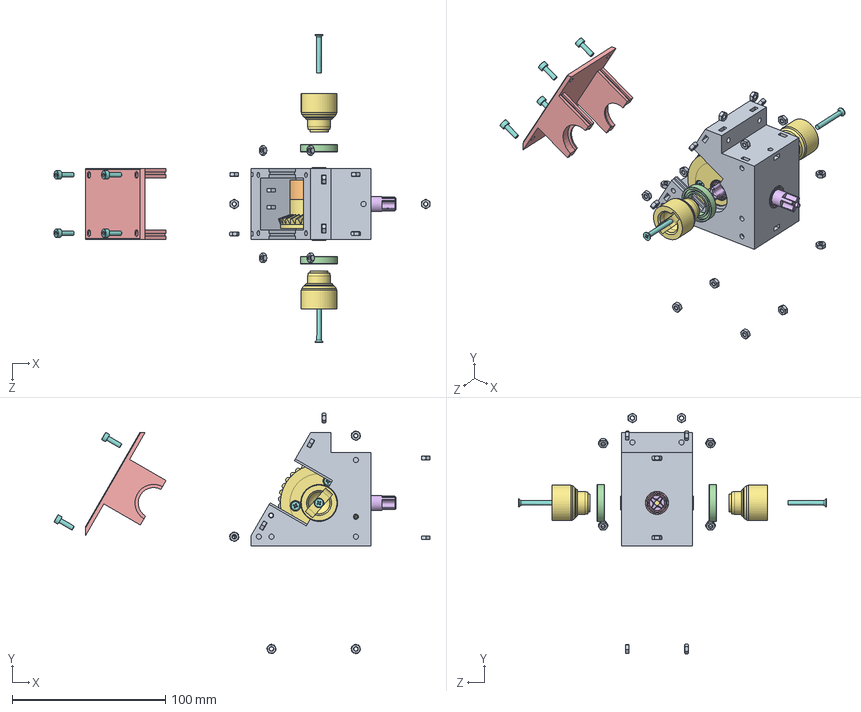
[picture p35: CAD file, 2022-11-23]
SOLIDWORKS 2019 FILES/differential-assy.SLDASM
245.1 x 156.9 x 200.8 mm
differential-box
differential-housing-a
planet-gear-pin x 6
planet-gear x 6
6700 - 15x10x4 Bearing x 3
shaft-gear x 2
differential-housing-b
countersunk flat head cross recess screw_iso x 5
hex nut style 1 gradeab_iso x 24
torque nut 08_iso x 2
plain washer normal grade a_iso x 12
radial ball bearing_68_iso x 2
differential-box-lid
drive-pinion-gear
wheel-shaft-housing x 2
socket head cap screw_iso x 4

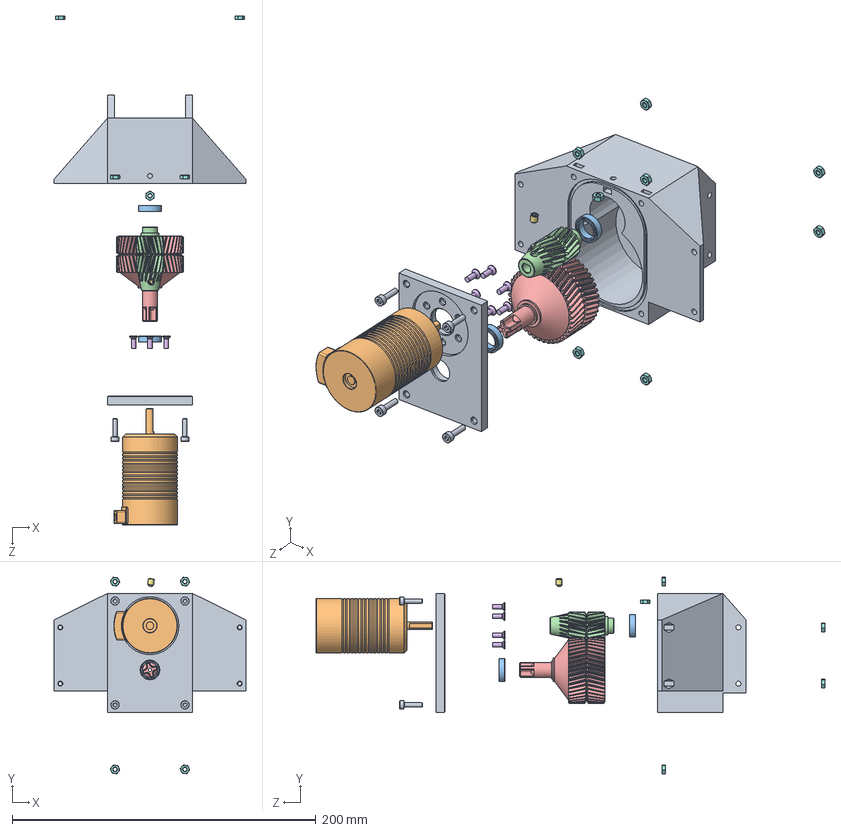
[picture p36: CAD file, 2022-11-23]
SOLIDWORKS 2019 FILES/gear-box-assy.SLDASM
126.0 x 129.4 x 334.9 mm
gear-box x 2
3660-BLDC-RC-MOTOR
6700 - 15x10x4 Bearing x 2
sg-16-1
sg-42-1
countersunk flat head cross recess screw_iso x 6
socket set screw cup point_iso
hex nut style 1 gradeab_iso x 9
socket head cap screw_iso x 4

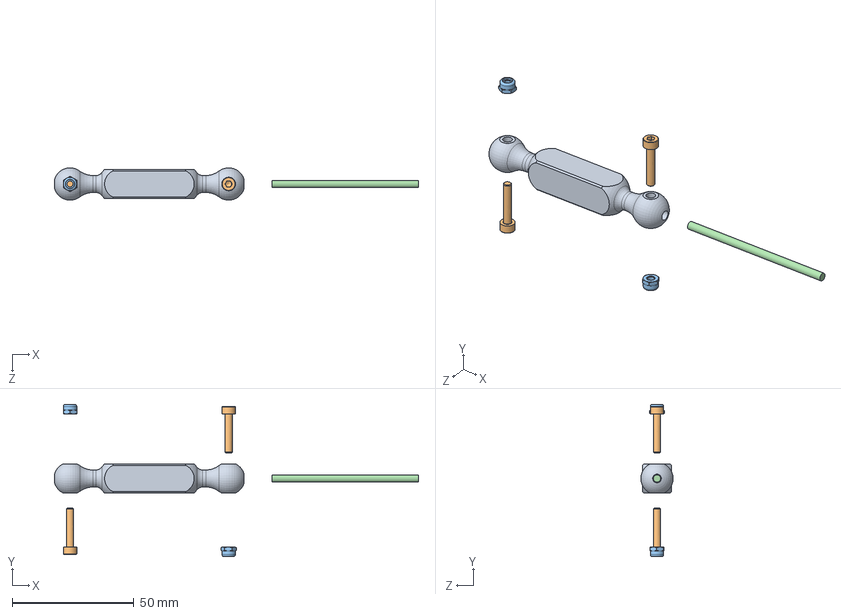
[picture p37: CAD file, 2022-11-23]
SOLIDWORKS 2019 FILES/wheel-shaft-assy.SLDASM
149.2 x 62.4 x 13.2 mm
wheel-shaft
socket head cap screw_iso x 2
torque nut 08_iso x 2
wheel-shaft-strength-bar

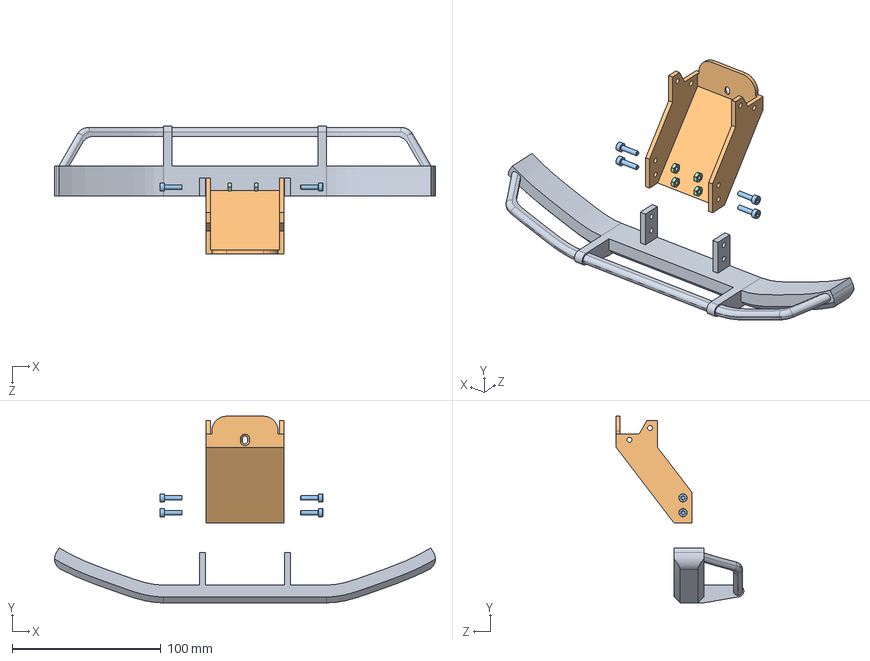
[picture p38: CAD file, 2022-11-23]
SOLIDWORKS 2019 FILES/bumper-front.SLDASM
256.3 x 125.7 x 86.0 mm
bumper-bottom-front
bumper-bracket-front
socket head cap screw_iso x 4
hex nut style 1 gradeab_iso x 4

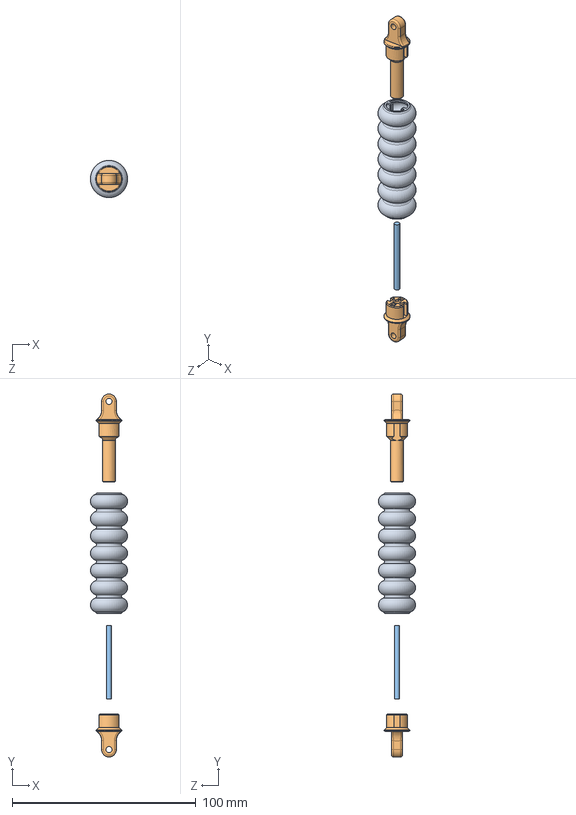
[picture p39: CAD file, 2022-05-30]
SOLIDWORKS 2019 FILES/shock-assy-V2.SLDASM
20.3 x 197.6 x 20.3 mm
tpu-spring
shock-eye x 2
shock-pin

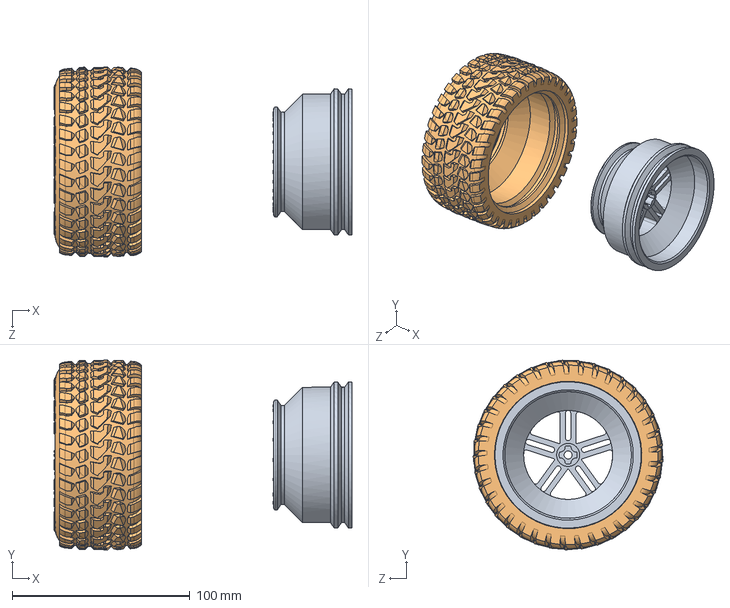
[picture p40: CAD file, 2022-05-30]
SOLIDWORKS 2019 FILES/wheel-assy.SLDASM
167.5 x 106.7 x 106.7 mm
rim
tire

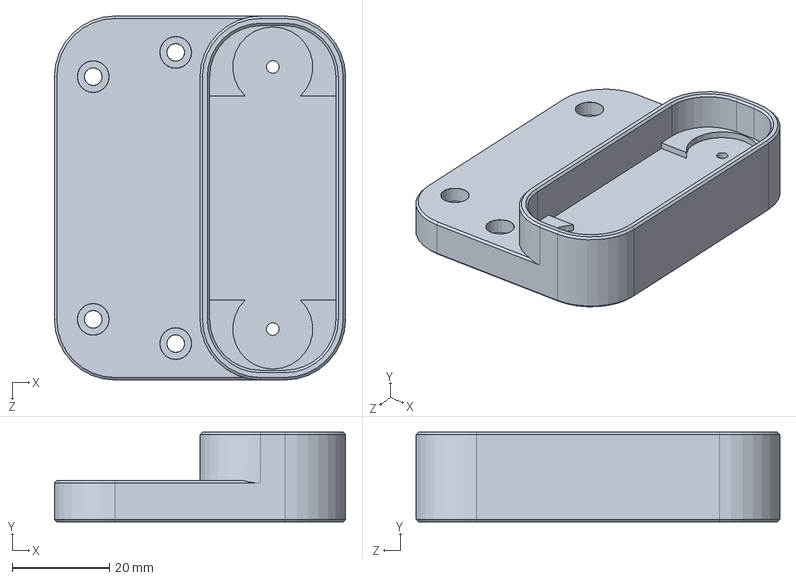
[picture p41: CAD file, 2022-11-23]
SOLIDWORKS 2019 FILES/body-mount-rear.SLDPRT
60.0 x 18.5 x 75.0 mm

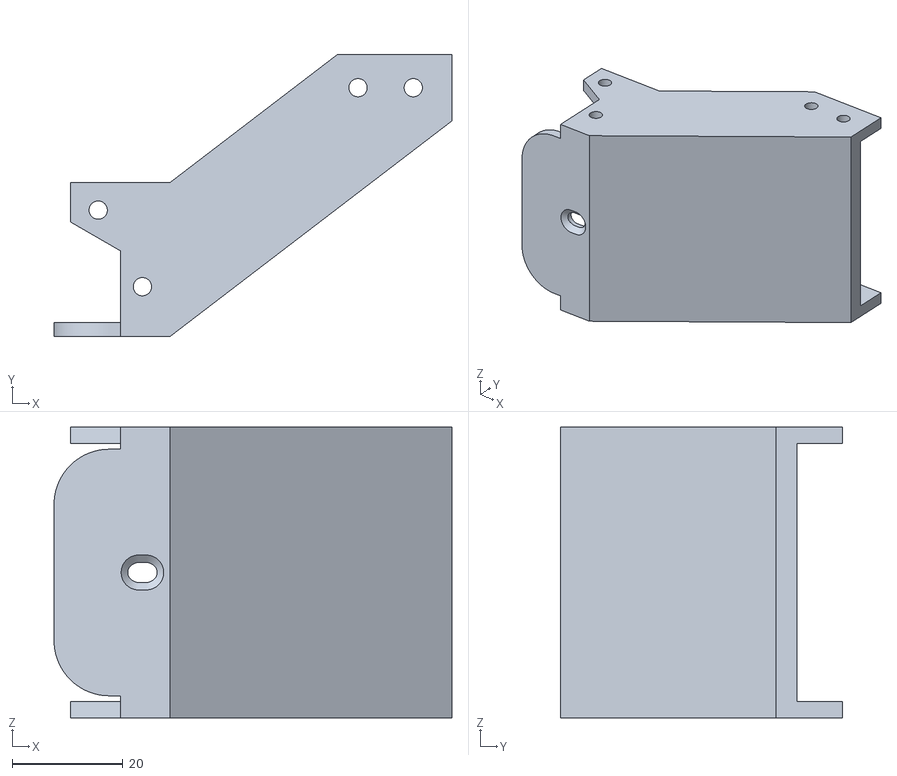
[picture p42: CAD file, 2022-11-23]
STL/chassis/bumper-bracket-front.STL
72.0 x 51.0 x 52.6

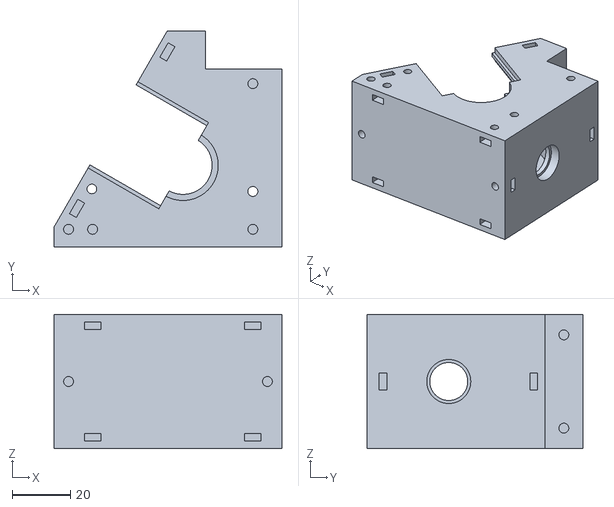
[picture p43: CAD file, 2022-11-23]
STL/differential/differential-box.STL
78.2 x 74.0 x 46.0

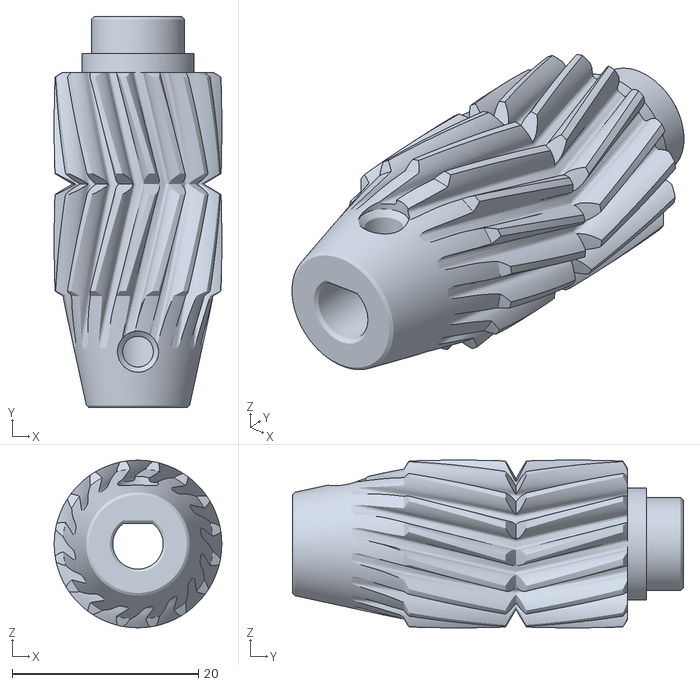
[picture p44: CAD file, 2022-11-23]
STL/drivetrain/sg-16-1-lowres.stl
18.0 x 42.0 x 18.0

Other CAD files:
STL/extras/cycplus g1 bracket.STL
STL/steering/steering-knuckle-right.STL
STL/suspension/shock-tower-back.STL
SOLIDWORKS 2019 FILES/body-mount-front.SLDPRT
SOLIDWORKS 2019 FILES/3660-BLDC-RC-MOTOR.SLDPRT
SOLIDWORKS 2019 FILES/6700 - 15x10x4 Bearing.sldprt
SOLIDWORKS 2019 FILES/SERVO HORN, METAL, 25T, BLUE-V2.SLDPRT
SOLIDWORKS 2019 FILES/TOWER PRO MG-995, ANALOG SERVO, BODY, BOTTOM-V2.SLDPRT
SOLIDWORKS 2019 FILES/TOWER PRO MG-995, ANALOG SERVO, BODY, MIDDLE-V2.SLDPRT
SOLIDWORKS 2019 FILES/TOWER PRO MG-995, ANALOG SERVO, BODY, TOP-V2.SLDPRT
SOLIDWORKS 2019 FILES/TOWER PRO MG-995, ANALOG SERVO, CONNECTOR-V2.SLDPRT
SOLIDWORKS 2019 FILES/TOWER PRO MG-995, ANALOG SERVO, HORN-V2.SLDPRT
SOLIDWORKS 2019 FILES/TOWER PRO MG-995, ANALOG SERVO, SHAFT-V2.SLDPRT
SOLIDWORKS 2019 FILES/axle.SLDPRT
SOLIDWORKS 2019 FILES/back-assy.SLDDRW
SOLIDWORKS 2019 FILES/body-mount-front-body-bracket.SLDPRT
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

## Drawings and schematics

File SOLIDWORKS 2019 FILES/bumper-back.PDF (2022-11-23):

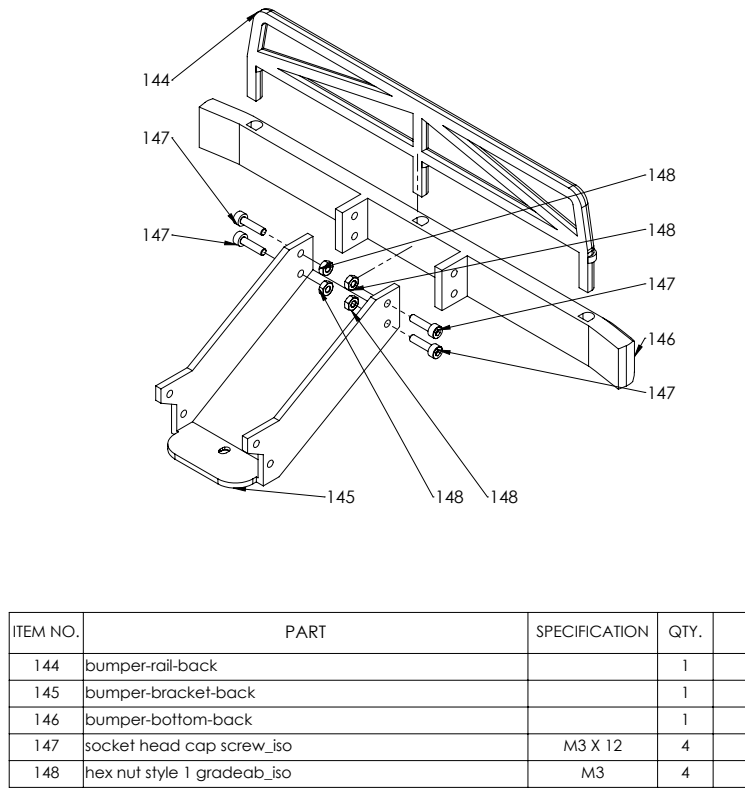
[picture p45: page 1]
ITEM NO.; PART; SPECIFICATION; QTY.; SW-Configuration; socket head cap screw_iso; ISO 4762 M3 x 12 - 12N; hex nut style 1 gradeab_iso; ISO - 4032 - M3 - D - N

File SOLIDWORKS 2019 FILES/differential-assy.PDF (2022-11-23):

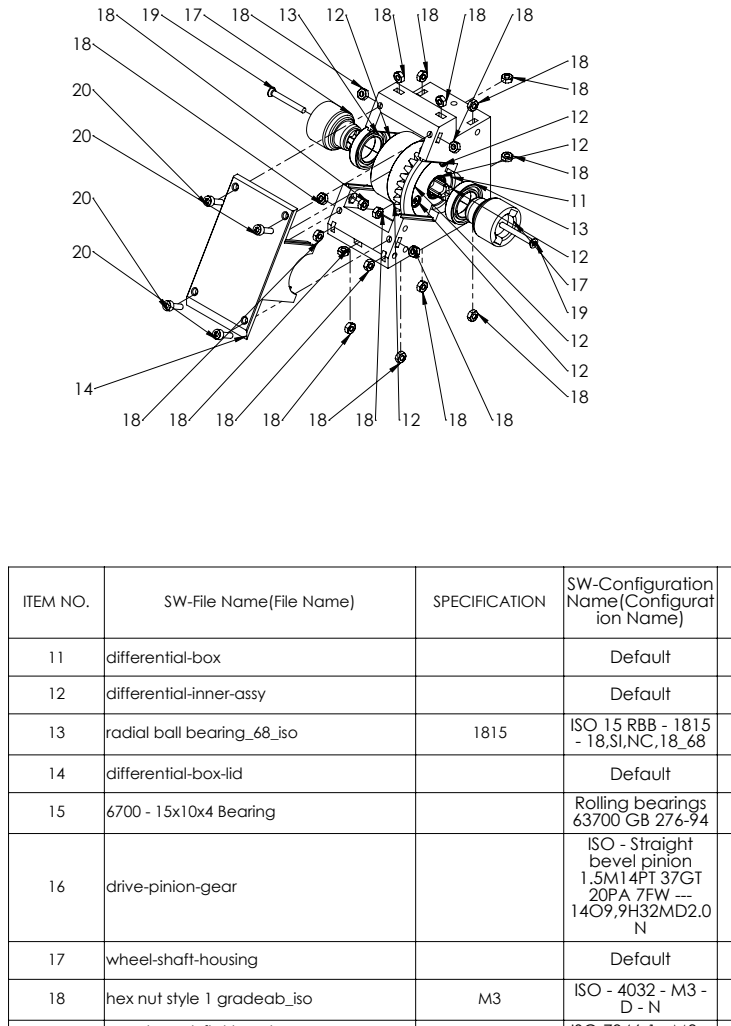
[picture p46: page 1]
ITEM NO.; SW-File Name(File Name); SPECIFICATION; ion Name); radial ball bearing_68_iso; ISO 15 RBB - 1815; 6700 - 15x10x4 Bearing; Rolling bearings; ISO - Straight bevel pinion 1.5M14PT 37GT 20PA 7FW ---; hex nut style 1 gradeab_iso; ISO - 4032 - M3 -; countersunk flat head cross recess; screw_iso; ISO 7046-1 - M3 x

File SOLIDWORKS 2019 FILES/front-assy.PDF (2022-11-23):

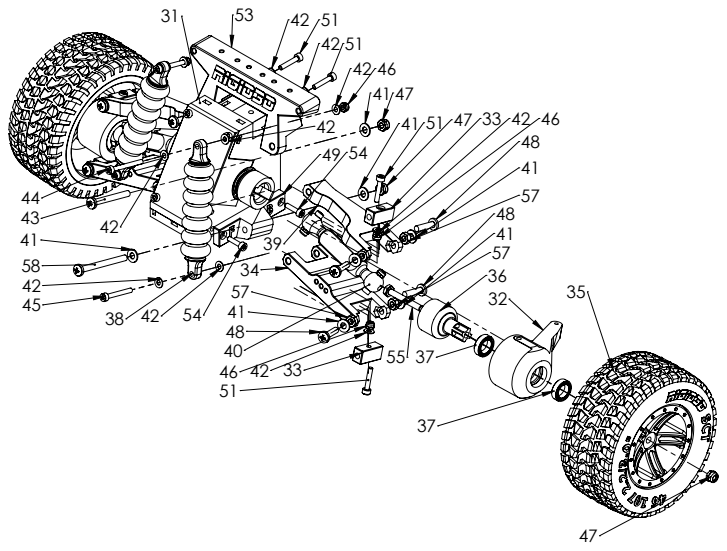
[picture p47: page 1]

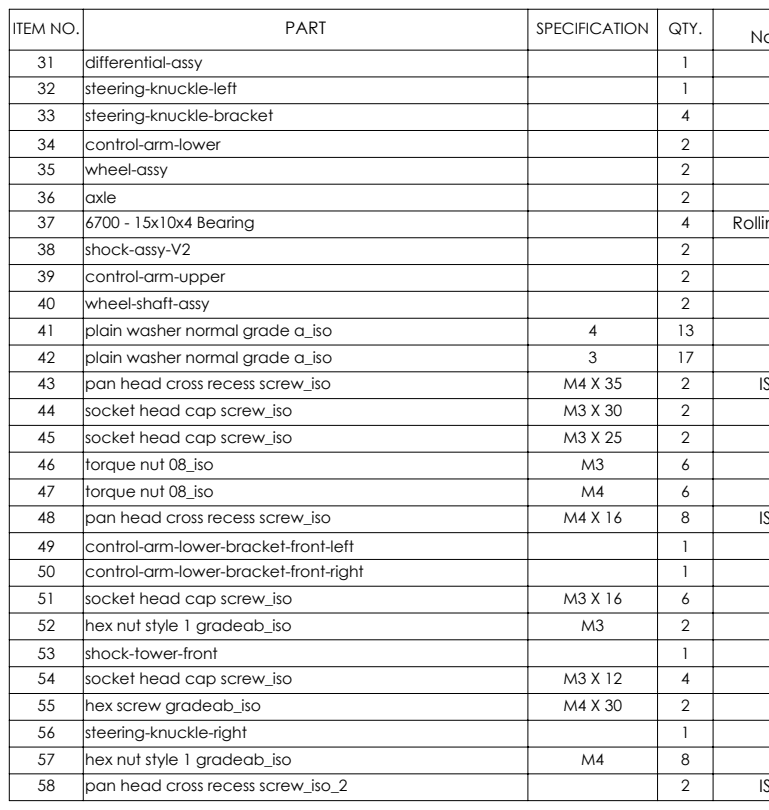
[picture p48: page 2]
ITEM NO.; PART; SPECIFICATION QTY.; SW-Configuration; 6700 - 15x10x4 Bearing; Rolling bearings 63700 GB 276-94; plain washer normal grade a_iso; Washer ISO 7089 - 4; Washer ISO 7089 - 3; pan head cross recess screw_iso; ISO 7045 - M4 x 35 - Z - 35N; socket head cap screw_iso; ISO 4762 M3 x 30 - 18N; ISO 4762 M3 x 25 - 18N; torque nut 08_iso; ISO 10511-M3-N; ISO 10511-M4-N; ISO 7045 - M4 x 16 - Z - 16N; ISO 4762 M3 x 16 - 16N; hex nut style 1 gradeab_iso; ISO - 4032 - M3 - D - N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

Name(Configuration Name)

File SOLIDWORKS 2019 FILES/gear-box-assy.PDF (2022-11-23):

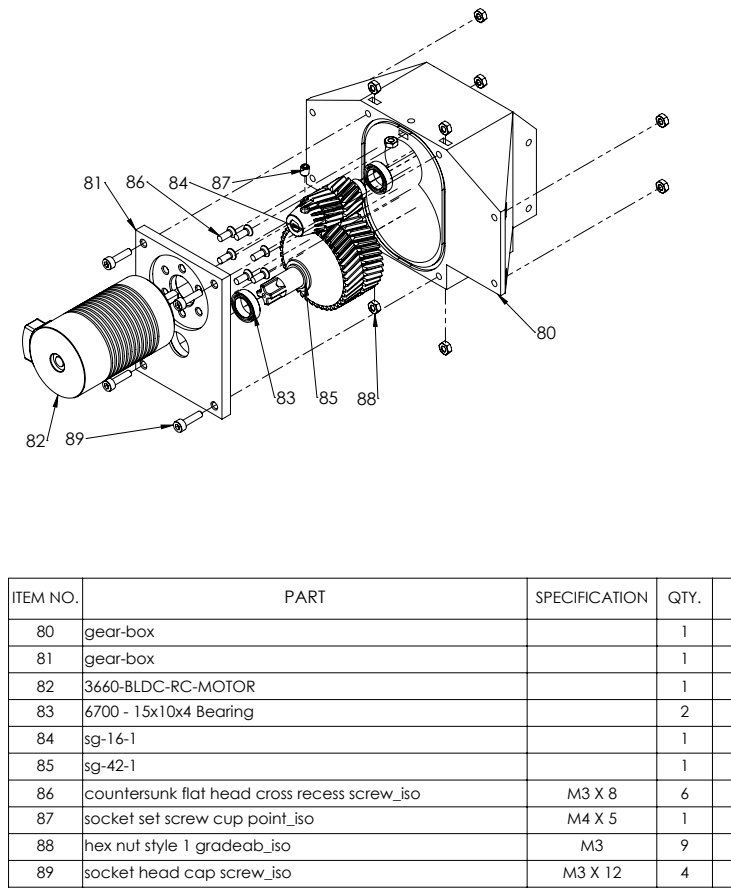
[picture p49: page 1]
ITEM NO.; PART; SPECIFICATION; QTY.; SW-Configuration; 6700 - 15x10x4 Bearing; Rolling bearings 63700 GB 276-94; countersunk flat head cross recess screw_iso; ISO 7046-1 - M3 x 8 - Z - 8N; socket set screw cup point_iso; ISO 4029 - M4 x 5-N; hex nut style 1 gradeab_iso; ISO - 4032 - M3 - D - N; socket head cap screw_iso; ISO 4762 M3 x 12 - 12N

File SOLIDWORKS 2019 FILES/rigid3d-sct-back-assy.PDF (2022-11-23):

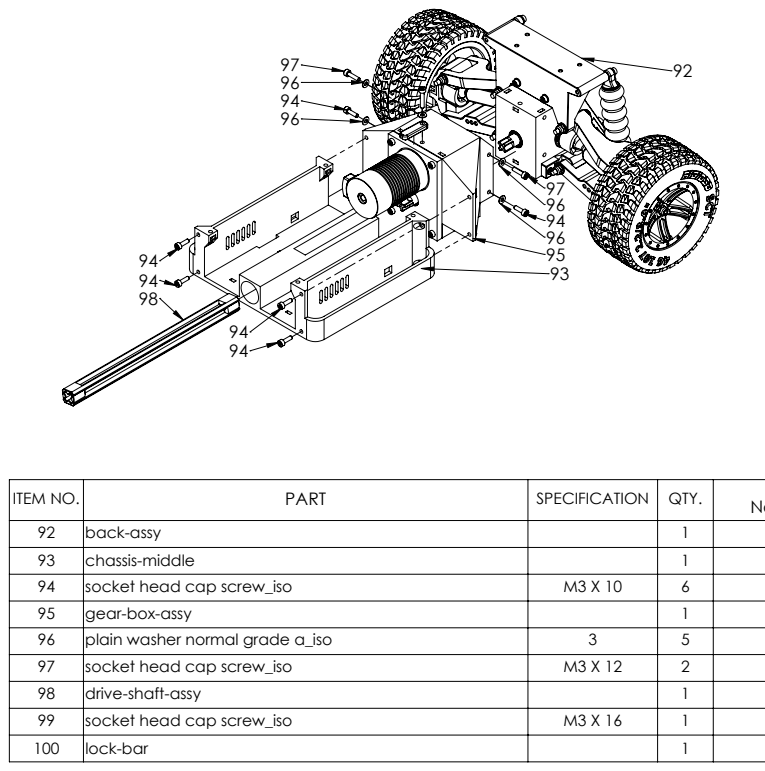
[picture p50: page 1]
ITEM NO.; PART; SPECIFICATION; QTY.; SW-Configuration; socket head cap screw_iso; ISO 4762 M3 x 10 - 10N; plain washer normal grade a_iso; Washer ISO 7089 - 3; ISO 4762 M3 x 12 - 12N; ISO 4762 M3 x 16 - 16N

Name(Configuration Name)

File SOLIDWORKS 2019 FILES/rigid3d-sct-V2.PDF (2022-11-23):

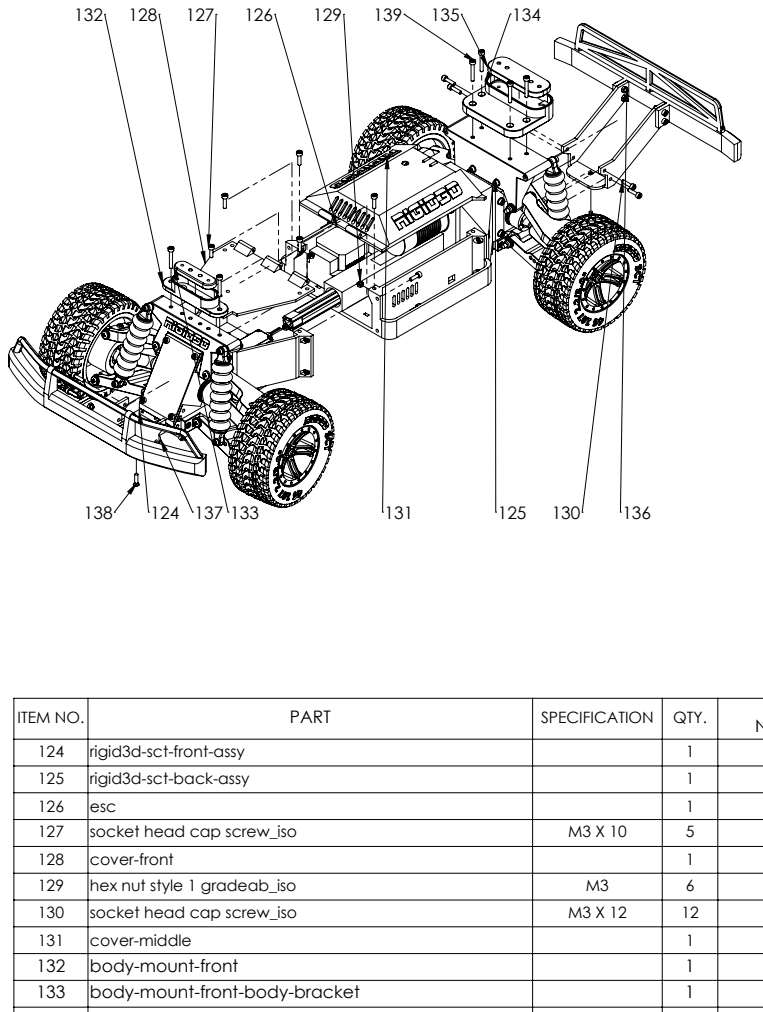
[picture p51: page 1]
ITEM NO.; PART; SPECIFICATION; QTY.; SW-Configuration; socket head cap screw_iso; ISO 4762 M3 x 10 - 10N; hex nut style 1 gradeab_iso; ISO - 4032 - M3 - D - N; ISO 4762 M3 x 12 - 12N; 134 body-mount-rear; Default

Name(Configuration Name)

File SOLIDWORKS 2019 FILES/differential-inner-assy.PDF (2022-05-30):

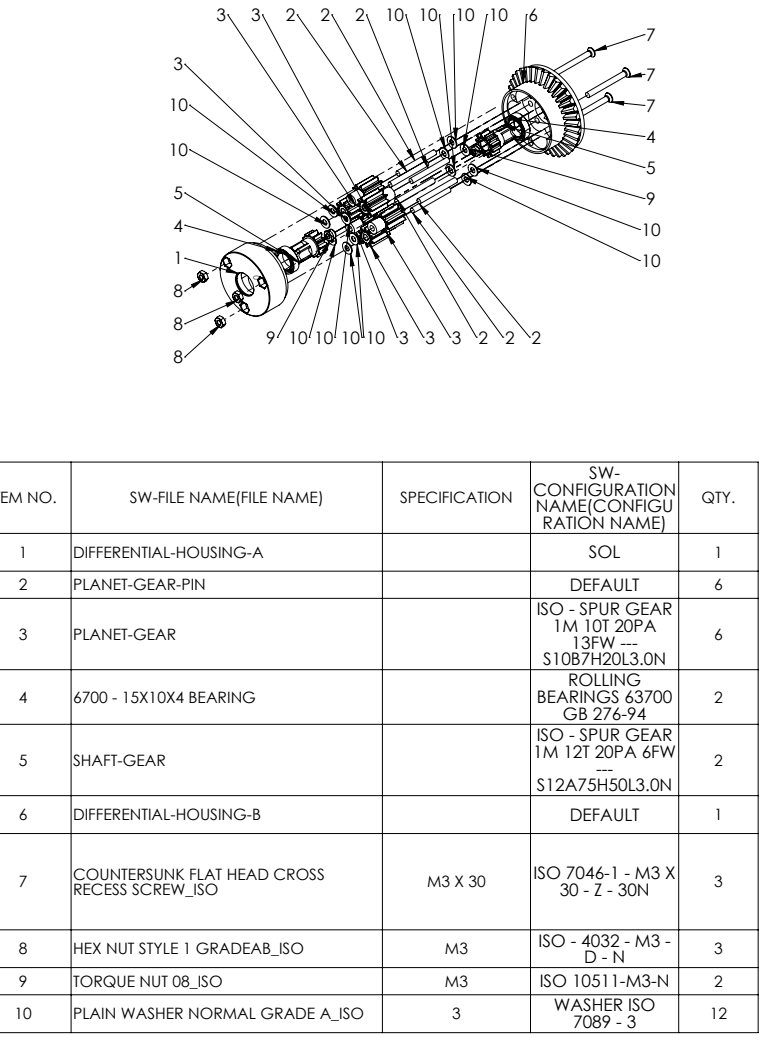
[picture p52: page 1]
ITEM NO.; SW-FILE NAME(FILE NAME); SPECIFICATION; RATION NAME); ISO - SPUR GEAR 1M 10T 20PA 13FW ---; 6700 - 15X10X4 BEARING; BEARINGS 63700 GB 276-94 ISO - SPUR GEAR 1M 12T 20PA 6FW --- S12A75H50L3.0N; COUNTERSUNK FLAT HEAD CROSS; RECESS SCREW_ISO; ISO 7046-1 - M3 X; HEX NUT STYLE 1 GRADEAB_ISO; ISO - 4032 - M3 -; TORQUE NUT 08_ISO; ISO 10511-M3-N; PLAIN WASHER NORMAL GRADE A_ISO; WASHER ISO

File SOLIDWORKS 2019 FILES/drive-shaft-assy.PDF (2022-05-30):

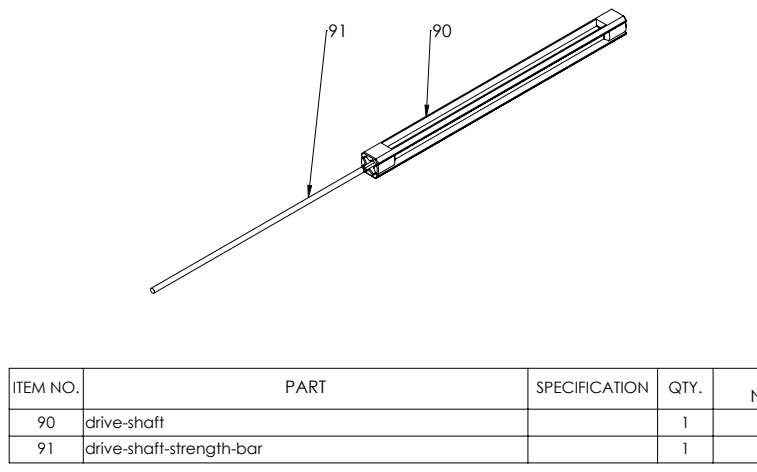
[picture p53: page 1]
ITEM NO.; PART; SPECIFICATION; QTY.; SW-Configuration

Name(Configuration Name)

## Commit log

2022-05-30 Initial Release
    [3660-BLDC-RC-MOTOR.SLDPRT, 6700 - 15x10x4 Bearing.sldprt, BACK-ASSY-BOM.xlsx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]
2022-06-13 Lowres Gear Stls and Photo
    [sg-16-1-lowres.stl, sg-42-1-lowres.stl]
2022-11-23 Bumpers & Body Mounts Release
    [BUMPER-BACK-ASSY-BOM.xlsx, BUMPER-FRONT-ASSY-BOM.xlsx, DIFFERENTIAL-ASSY-BOM.xlsx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]
